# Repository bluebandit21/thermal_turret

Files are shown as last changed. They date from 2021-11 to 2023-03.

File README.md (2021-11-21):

Thermal Turret Project

#### **Useful documentation:**
SEN-09570 Infrared Thermometer: 
[Datasheet](https://www.sparkfun.com/datasheets/Sensors/Temperature/SEN-09570-datasheet-3901090614M005.pdf)

mediapipe 0.8.3.1 download link: https://pypi.org/project/mediapipe/0.8.3.1/#files

pip install some-package.whl

https://github.com/jiuqiant/mediapipe_python_aarch64

https://forums.developer.nvidia.com/t/google-mediapipe-real-time-hand-tracking-on-nano/80281/6

https://github.com/yockgen/mediapipe_jetson_nano

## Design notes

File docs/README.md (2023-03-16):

# Thermal Turret

This is a project developed as a proof of concept to a thermometer that can recognize human faces and direct a thermal laser at the forehead to measure the temperature of the person. This was initially built during the 2019 Covid19 Pandemic but has since been replaced by better systems and designs into 2020 and 2021.

All links to important documentation are located in [development-references](/docs/development-references.md)

## Basic Hardware Diagram

A more  thorough wiring sheet with descriptions and pins can be found in the [wiring](/docs/wiring.md) page

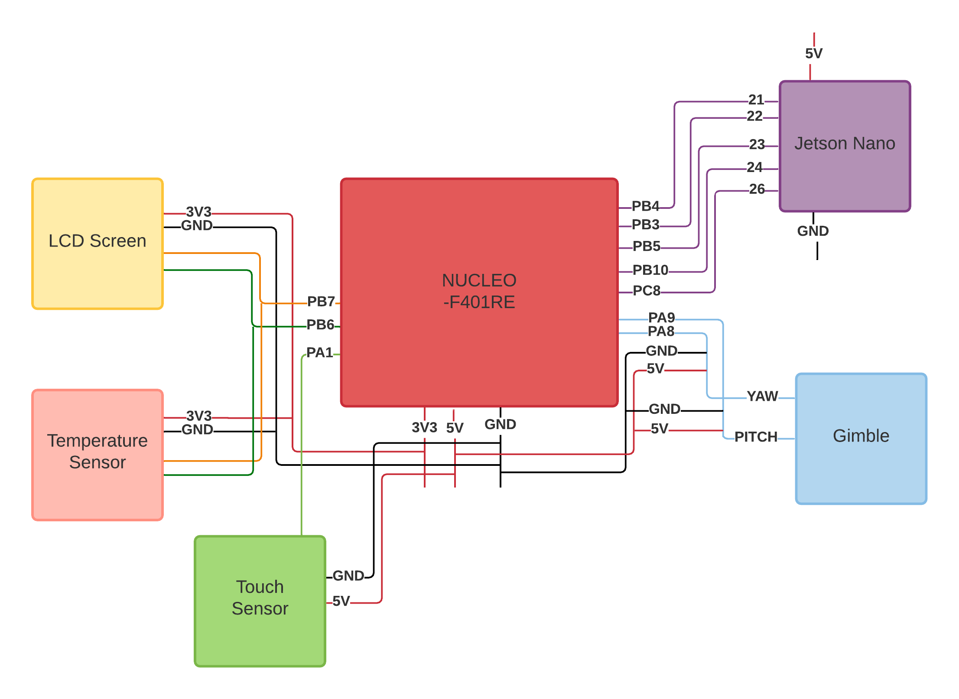
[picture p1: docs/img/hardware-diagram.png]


## Components and Codebase

### Infrared Thermometer
The thermal turret uses off the shelf consumer parts including a SEN-09570 infrared thermometer from sparkfun in a 3d printed case which can be foung in the [/cad](/cad) folder. The basic functionality can be seen by using the arduino project in the [/misc](/misc) folder. It also gives all information for locations of memory and important communication addresses for the temperature sensor.

There is also a TMP36 touch sensor for more fine tuned temperature readings in this specific prototype. When building the final prototype this is expected to be removed. It is added at this moment to compare between the SEN-09570 and itself for accuracy testing of the SEN-09570.

### Microcontroller
The microcontroller on this device is an STM32F401RETX nucleo development board. You can use the standard CubeMX IDE to compile and build the project on the nucleo seamlessly. You can follow the [wiring diagram](/docs/wiring.md) to see how to link all parts of the project. 

### Computer Vision

The computer vision device is a Jetson Nano. The developer kit which aided in cooling and running the jetson at high speeds. One can replace this with a suitable heat sink and fan combination. It uses OpenCV and a precompiled neural network for recognizing faces. There is a crontab to run the openCV script on startup as to not need setup beforehand. There is also a display linked to the Jetson Nano to display the view to the user. The Jetson Nano links with the Nucleo board by a parallel bus.

### Serial LCD

There is a serial LCD with RGB backlight linked with the project to display the temperature and other information. The reason for the RGB backlight is so that a user can see at a glance wether they are allowed to pass. The LCD will go green for safe temperatures, yellow if it wants to test you with the touch sensor and red if your temperature is obviously too high. 

## Basic Code Flow

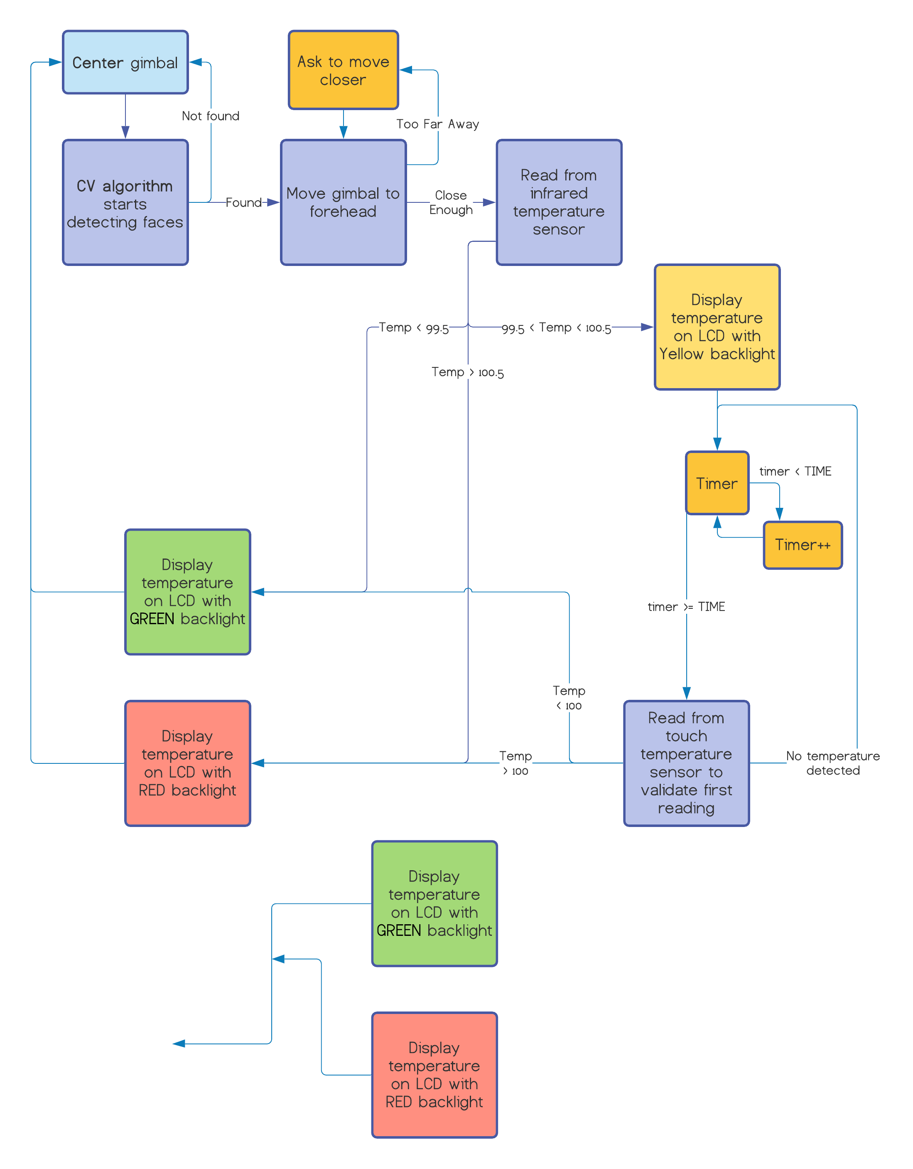
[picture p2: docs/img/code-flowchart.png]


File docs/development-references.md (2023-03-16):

#### **Useful documentation:**
SEN-09570 Infrared Thermometer: 
[Datasheet](https://www.sparkfun.com/datasheets/Sensors/Temperature/SEN-09570-datasheet-3901090614M005.pdf)

#### **Misc CV stuff:**

mediapipe 0.8.3.1 download link: https://pypi.org/project/mediapipe/0.8.3.1/#files

pip install some-package.whl

https://github.com/jiuqiant/mediapipe_python_aarch64

https://forums.developer.nvidia.com/t/google-mediapipe-real-time-hand-tracking-on-nano/80281/6

https://github.com/yockgen/mediapipe_jetson_nano

#### HEL_BUSY Fix
https://stackoverflow.com/questions/330793/how-to-initialize-a-struct-in-accordance-with-c-programming-language-standards

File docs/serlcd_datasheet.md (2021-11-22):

# LCD Codes for SparkFun RGB 3.3v Serial Open LCD display 
### with an attached Qwiic adapter

Rearranged for viewing by: Andrew Kent

Original information copied from SerLCD:
By: Gaston R. Williams

Original information copied from OpenLCD:
The OpenLCD display information is based based on code by
Nathan Seidle

## Addresses

Please Note: 0x72 is the 7-bit I2C address. If you are using a different language than Arduino you will probably
need to add the Read/Write bit to the end of the address. This means the default read address for the OpenLCD
is 0b.1110.0101 or 0xE5 and the write address is 0b.1110.0100 or 0xE4.

For more information see https://learn.sparkfun.com/tutorials/i2c
Note: This information expects the display to be listening at the default I2C address. If your display is not at 0x72, you can
do a hardware reset. Tie the RX pin to ground and power up OpenLCD. You should see the splash screen
then "System reset Power cycle me" and the backlight will begin to blink. Now power down OpenLCD and remove
the RX/GND jumper. OpenLCD is now reset.

To get this code to work, attach a Qwiic adapter to an OpenLCD. Use the Qwiic cable to attach adapter to a SparkFun Blackboard or
an Arduino Uno with the Qwiic shield.

 The OpenLCD has 4.7k pull up resistors on SDA and SCL. If you have other devices on the
 I2C bus then you may want to disable the pull up resistors by clearing the PU (pull up) jumper.

OpenLCD will work at 400kHz Fast I2C. Use the .setClock() call shown below to set the data rate
faster if needed.

## Command cheat sheet:

|  ASCII | DEC | HEX |
| :----: | :--- | :--- |
|  \| |  124 | 0x7C - Put into setting mode |
| Ctrl+c | 3 | 0x03 - Change width to 20 |
| Ctrl+d | 4 | 0x04 - Change width to 16 |
| Ctrl+e | 5 | 0x05 - Change lines to 4 |
| Ctrl+f | 6 | 0x06 - Change lines to 2 |
| Ctrl+g | 7 | 0x07 - Change lines to 1 |
| Ctrl+h | 8 | 0x08 - Software reset of the system |
| Ctrl+i | 9 | 0x09 - Enable/disable splash screen |
| Ctrl+j | 10 | 0x0A - Save currently displayed text as splash |
| Ctrl+k | 11 | 0x0B - Change baud to 2400bps |
| Ctrl+l | 12 | 0x0C - Change baud to 4800bps |
| Ctrl+m | 13 | 0x0D - Change baud to 9600bps |
| Ctrl+n | 14 | 0x0E - Change baud to 14400bps |
| Ctrl+o | 15 | 0x0F - Change baud to 19200bps |
| Ctrl+p | 16 | 0x10 - Change baud to 38400bps |
| Ctrl+q | 17 | 0x11 - Change baud to 57600bps |
| Ctrl+r | 18 | 0x12 - Change baud to 115200bps |
| Ctrl+s | 19 | 0x13 - Change baud to 230400bps |
| Ctrl+t | 20 | 0x14 - Change baud to 460800bps |
| Ctrl+u | 21 | 0x15 - Change baud to 921600bps |
| Ctrl+v | 22 | 0x16 - Change baud to 1000000bps |
| Ctrl+w | 23 | 0x17 - Change baud to 1200bps |
| Ctrl+x | 24 | 0x18 - Change the contrast. Follow Ctrl+x with number 0 to 255. 120 is default. |
| Ctrl+y | 25 | 0x19 - Change the TWI address. Follow Ctrl+x with number 0 to 255. 114 (0x72) is default. |
| Ctrl+z | 26 | 0x1A - Enable/disable ignore RX pin on startup (ignore emergency reset) |
|  + | 43 | 0x2B - Set RGB backlight with three following bytes, 0-255 |
|  , | 44 | 0x2C - Display current firmware version |
|  - | 45 | 0x2D - Clear display. Move cursor to home position. |
|  . | 46 | 0x2E - Enable system messages (ie, display 'Contrast: 5' when changed) |
|  / | 47 | 0x2F - Disable system messages (ie, don't display 'Contrast: 5' when changed) |
|  0 | 48 | 0x30 - Enable splash screen |
|  1 | 49 | 0x31 - Disable splash screen |
| | 128-157 | 0x80-0x9D - Set the primary backlight brightness. 128 = Off, 157 = 100%. |
| | 158-187 | 0x9E-0xBB - Set the green backlight brightness. 158 = Off, 187 = 100%. |
| | 188-217 | 0xBC-0xD9 - Set the blue backlight brightness. 188 = Off, 217 = 100%. |

For example, to change the baud rate to 115200 send 124 followed by 18.

## All Commands

```cpp
#define DISPLAY_ADDRESS1 0x72 //This is the default address of the OpenLCD
#define MAX_ROWS 4
#define MAX_COLUMNS 20

//OpenLCD command characters
#define SPECIAL_COMMAND 254  //Magic number for sending a special command
#define SETTING_COMMAND 0x7C //124, |, the pipe character: The command to change settings: baud, lines, width, backlight, splash, etc

//OpenLCD commands
#define CLEAR_COMMAND 0x2D					//45, -, the dash character: command to clear and home the display
#define CONTRAST_COMMAND 0x18				//Command to change the contrast setting
#define ADDRESS_COMMAND 0x19				//Command to change the i2c address
#define SET_RGB_COMMAND 0x2B				//43, +, the plus character: command to set backlight RGB value
#define ENABLE_SYSTEM_MESSAGE_DISPLAY 0x2E  //46, ., command to enable system messages being displayed
#define DISABLE_SYSTEM_MESSAGE_DISPLAY 0x2F //47, /, command to disable system messages being displayed
#define ENABLE_SPLASH_DISPLAY 0x30			//48, 0, command to enable splash screen at power on
#define DISABLE_SPLASH_DISPLAY 0x31			//49, 1, command to disable splash screen at power on
#define SAVE_CURRENT_DISPLAY_AS_SPLASH 0x0A //10, Ctrl+j, command to save current text on display as splash

// special commands
#define LCD_RETURNHOME 0x02
#define LCD_ENTRYMODESET 0x04
#define LCD_DISPLAYCONTROL 0x08
#define LCD_CURSORSHIFT 0x10
#define LCD_SETDDRAMADDR 0x80

// flags for display entry mode
#define LCD_ENTRYRIGHT 0x00
#define LCD_ENTRYLEFT 0x02
#define LCD_ENTRYSHIFTINCREMENT 0x01
#define LCD_ENTRYSHIFTDECREMENT 0x00

// flags for display on/off control
#define LCD_DISPLAYON 0x04
#define LCD_DISPLAYOFF 0x00
#define LCD_CURSORON 0x02
#define LCD_CURSOROFF 0x00
#define LCD_BLINKON 0x01
#define LCD_BLINKOFF 0x00

// flags for display/cursor shift
#define LCD_DISPLAYMOVE 0x08
#define LCD_CURSORMOVE 0x00
#define LCD_MOVERIGHT 0x04
#define LCD_MOVELEFT 0x00

```

## Writing to the Display

```cpp
/*
 * Write a byte to the display.
 * Required for Print.
 */
size_t SerLCD::write(uint8_t b)
{
  beginTransmission(); // transmit to device
  transmit(b);
  endTransmission(); //Stop transmission
  delay(10);         // wait a bit
  return 1;
} // write

/*
 * Write a character buffer to the display.
 * Required for Print.
 */
size_t SerLCD::write(const uint8_t *buffer, size_t size)
{
  size_t n = 0;
  beginTransmission(); // transmit to device
  while (size--)
  {
    transmit(*buffer++);
    n++;
  }                  //while
  endTransmission(); //Stop transmission
  delay(10);         //
  return n;
} //write

/*
 * Write a string to the display.
 * Required for Print.
 */
size_t SerLCD::write(const char *str)
{
  if (str == NULL)
    return 0;
  return write((const uint8_t *)str, strlen(str));
}
```

## Example Functions

```cpp
#define SETTING_COMMAND    0x7C //124, |, the pipe character: The command to change settings: baud, lines, width, backlight, splash, etc
#define SET_RGB_COMMAND    0x2B				//43, +, the plus character: command to set backlight RGB value
#define SPECIAL_COMMAND    254  //Magic number for sending a special command
#define LCD_DISPLAYCONTROL 0x08
#define LCD_ENTRYMODESET   0x04
#define CLEAR_COMMAND      0x2D					//45, -, the dash character: command to clear and home the display

/*
 * Initialize the display
 *
 */
void SerLCD::init()
{
  beginTransmission();
  transmit(SPECIAL_COMMAND);                      //Send special command character
  transmit(LCD_DISPLAYCONTROL | _displayControl); //Send the display command
  transmit(SPECIAL_COMMAND);                      //Send special command character
  transmit(LCD_ENTRYMODESET | _displayMode);      //Send the entry mode command
  transmit(SETTING_COMMAND);                      //Put LCD into setting mode
  transmit(CLEAR_COMMAND);                        //Send clear display command
  endTransmission();                              //Stop transmission
  delay(50);                                      //let things settle a bit
} //init

// New backlight function
void SerLCD::setFastBacklight(unsigned long rgb)
{
  // convert from hex triplet to byte values
  byte r = (rgb >> 16) & 0x0000FF;
  byte g = (rgb >> 8) & 0x0000FF;
  byte b = rgb & 0x0000FF;

  //send commands to the display to set backlights
  beginTransmission();       // transmit to device
  transmit(SETTING_COMMAND); //Send special command character
  transmit(SET_RGB_COMMAND); //Send the set RGB character '+' or plus
  transmit(r);               //Send the red value
  transmit(g);               //Send the green value
  transmit(b);               //Send the blue value
  endTransmission();         //Stop transmission
  delay(10);
} // setFastBacklight

/*
 *  Move the cursor multiple characters to the left.
 *
 *  count byte - number of characters to move
 */
void SerLCD::moveCursorLeft(byte count)
{

  beginTransmission(); // transmit to device

  for (int i = 0; i < count; i++)
  {
    transmit(SPECIAL_COMMAND); //Send special command character
    transmit(0x10);         //Send command code
  }                            // for
  endTransmission();           //Stop transmission

  delay(50); //Wait a bit longer for special display commands
} // moveCursorLeft

/*
 *  Move the cursor one character to the right.
 */
void SerLCD::moveCursorRight()
{
  beginTransmission(); // transmit to device

  for (int i = 0; i < count; i++)
  {
    transmit(SPECIAL_COMMAND); //Send special command character
    transmit(0x14);         //Send command code
  }                            // for
  endTransmission();           //Stop transmission

  delay(50); //Wait a bit longer for special display commands

/*
 * Send the clear command to the display.  This clears the
 * display and forces the cursor to return to the beginning
 * of the display.
 */
void SerLCD::clear()
{
  beginTransmission();       // transmit to device
  transmit(SETTING_COMMAND); //Put LCD into setting mode
  transmit(CLEAR_COMMAND);         //Send the command code
  endTransmission();         //Stop transmission

  delay(10); //Hang out for a bit
  delay(10); // a little extra delay after clear
}

```

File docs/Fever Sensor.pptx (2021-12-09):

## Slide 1

FEVER SENSOR
Abdulqader Khidir, Andrew Kent, Andrew Plotner, Anjana Malayarasan, Rutvi Shah

Hardware

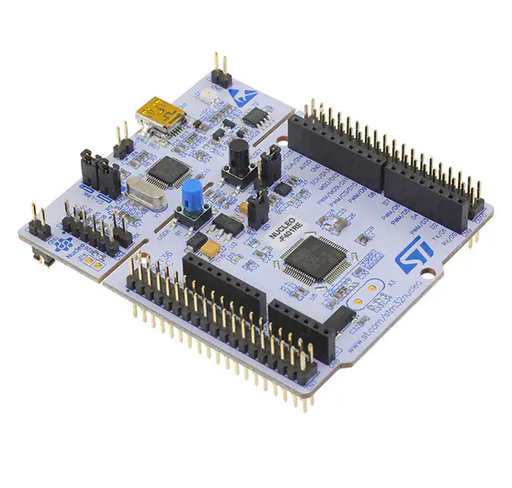
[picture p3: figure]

NUCLEO F401RE
STM32 microprocessor development board that controls the entire system. Takes input from camera/ Jetson Nano, and temperature sensors. Controls gimbal servos and sends output to displays.

Authors
Be proud of your work! Add the names of the people involved in this study. Don't forget to include titles and honorifics. We're proud of those too.

Affiliations
We're also proud of the institutions that we are with and support our research. Let's let them know by adding their names and logos here.

Research is often built on something that is already out there. Cite key references that you looked at while conducting your study.

Related literature

NVIDIA JETSON NANO
Small, powerful computer that controls the computer vision portion of the system. Detects the forehead and signals sensor.

Abstract

During the pandemic, taking human temperature readings from a distance is necessary in most establishments. Hiring to complete this task is costly and detrimental to workflow in job shortages. A device is being designed to test and verify users as they enter buildings or pass checkpoints. The device consists of a thermal sensor (Melexis MLX90614) and camera (Logitech C310) detecting human faces and following their movements using a 2 axis gimbal. When centered on a forehead, the thermal sensor reads and displays temperature data using a color LCD (Sparkfun LCD-16396). If the temperature is not satisfactory the system requires a user to hold a touch temperature sensor (Analog Devices TMP36) to get a more accurate reading of temperature. This approach improves accuracy and uniformity of temperature sensing and allows easy notice to interested parties of possibly hazardous associates.

Objective

Living in a time of a pandemic it is necessary to develop machines to improve the lives of others and keep the public safe. To reduce the staffing shortage in an impactful manner while keeping risk of exposure to a minimum.

Future Research

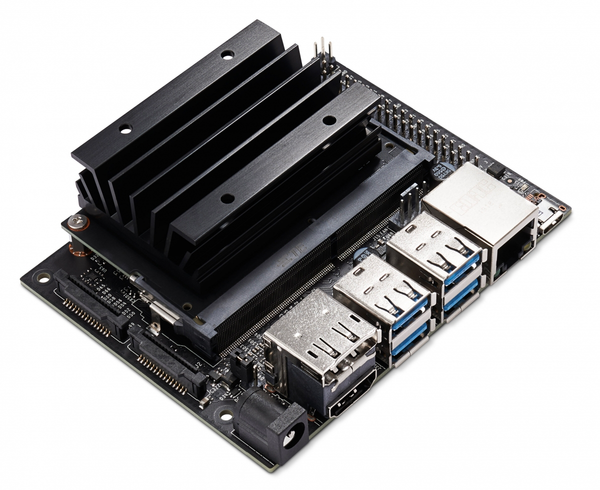
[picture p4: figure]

INFRARED TEMPERATURE SENSOR
No-contact Forehead Thermometer. Detects temperature and send output to microprocessor.

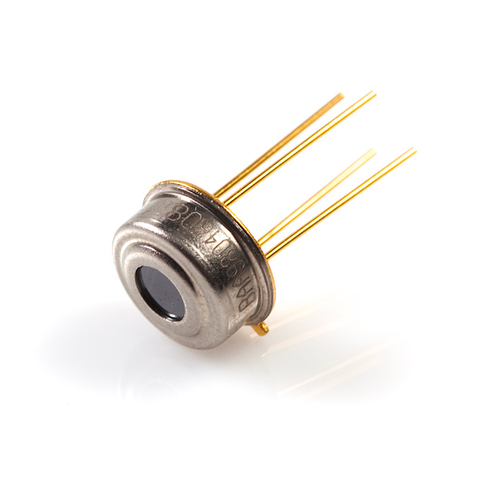
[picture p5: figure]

The need of long-range thermal sensors is of utmost importance, as it will allow medium to large scale testing of the system. A printed circuit board (PCB) for final connections is in development. Advancements in mounting hardware and case designs are necessary and are to reach further development after PCB design.

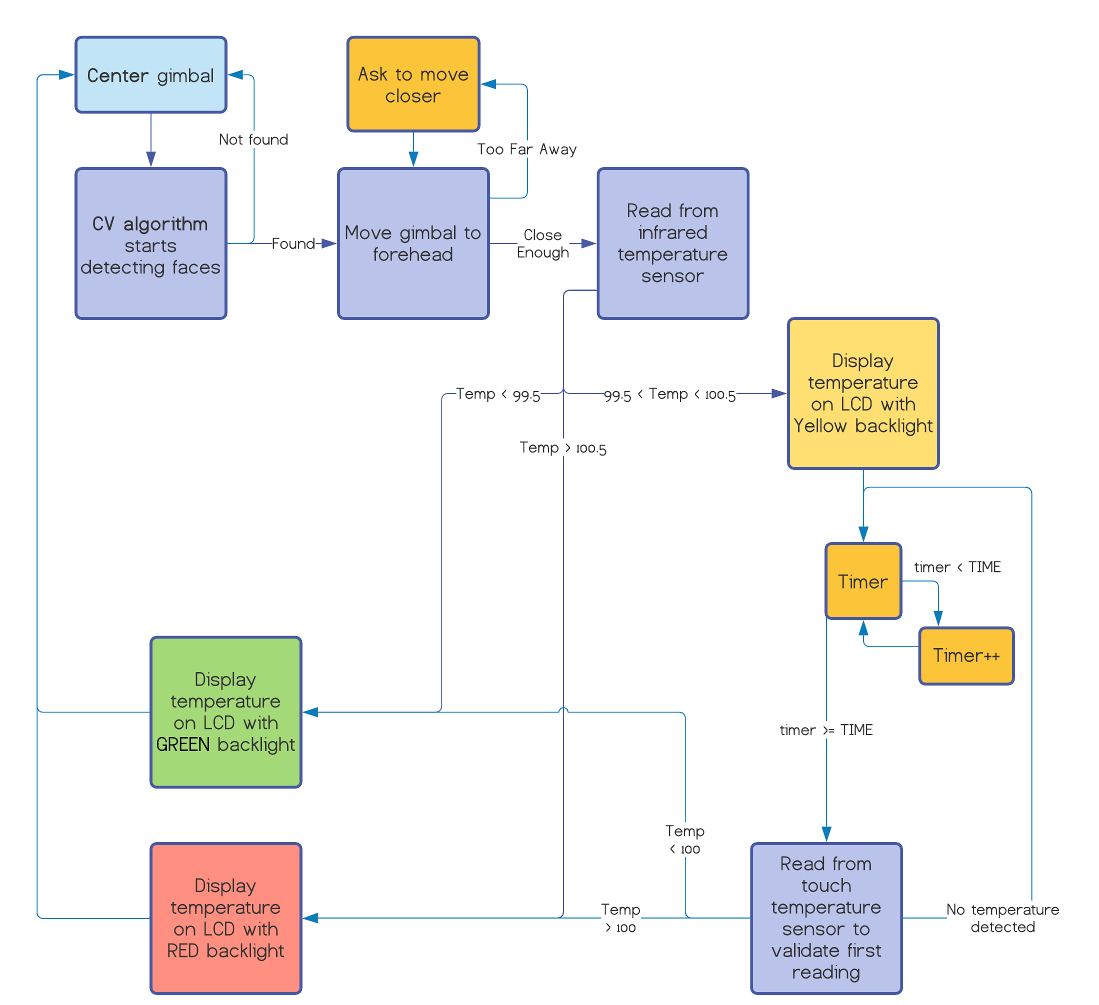
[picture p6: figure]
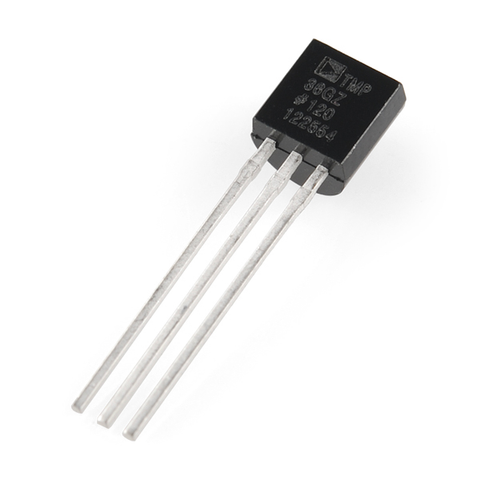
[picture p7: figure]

ANALOG CONTACT TEMPERATURE SENSOR
Touch temperature sensor provides voltage output proportional to the absolute temperature

SERVO GIMBAL
2-axis gimbal. Allows the camera to follow the movement of the person.

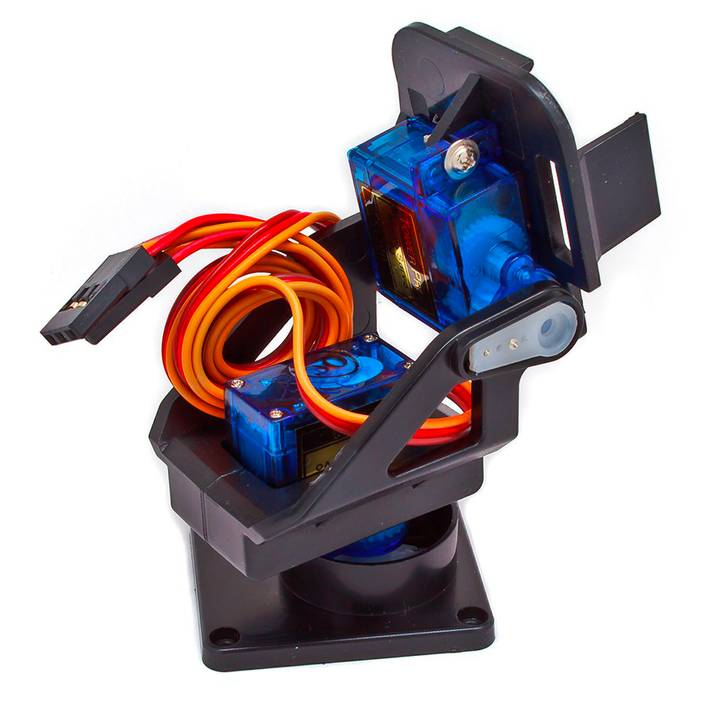
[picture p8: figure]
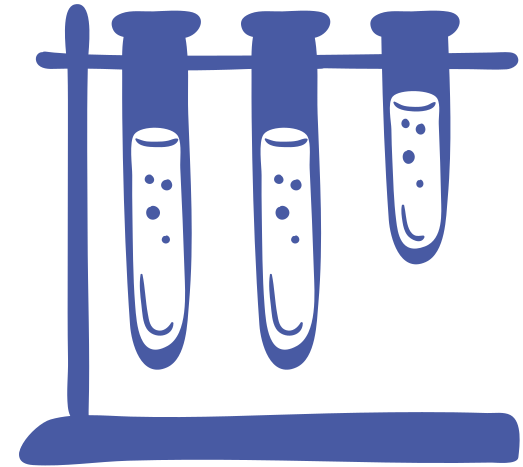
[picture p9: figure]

Code Logic

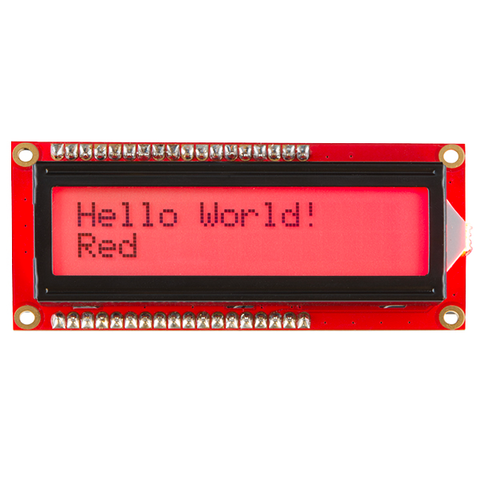
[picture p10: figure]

RGB LCD DISPLAY
Displays temperature and information in an easily visible format, also has a multicolor backlight to convey information at a glance.

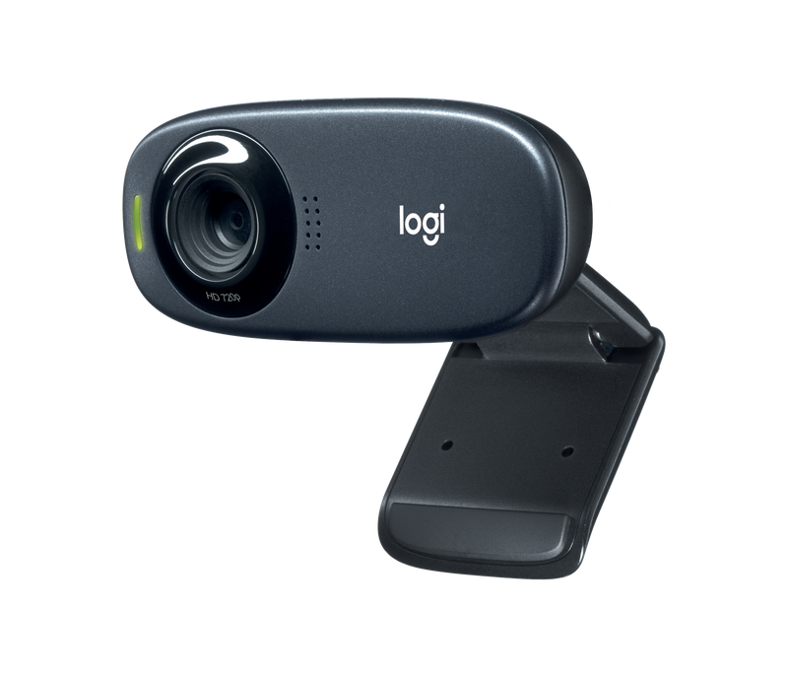
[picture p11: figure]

CAMERA
Allows the Jetson Nano to see the world around it and process human faces.

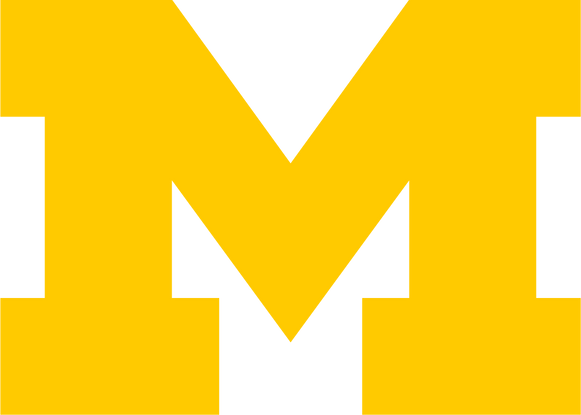
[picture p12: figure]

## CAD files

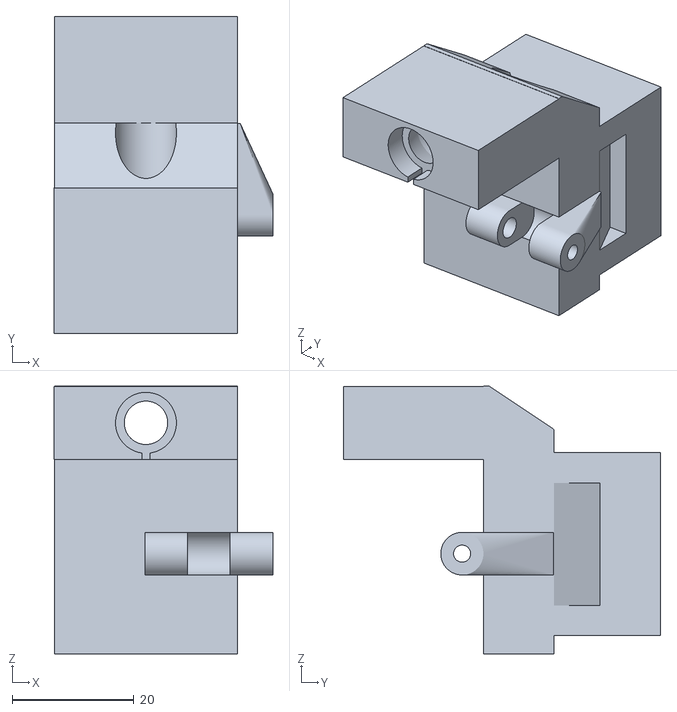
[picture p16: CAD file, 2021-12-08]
cad/stl/Full-test1 - v2.stl
35.9 x 52.1 x 44.0

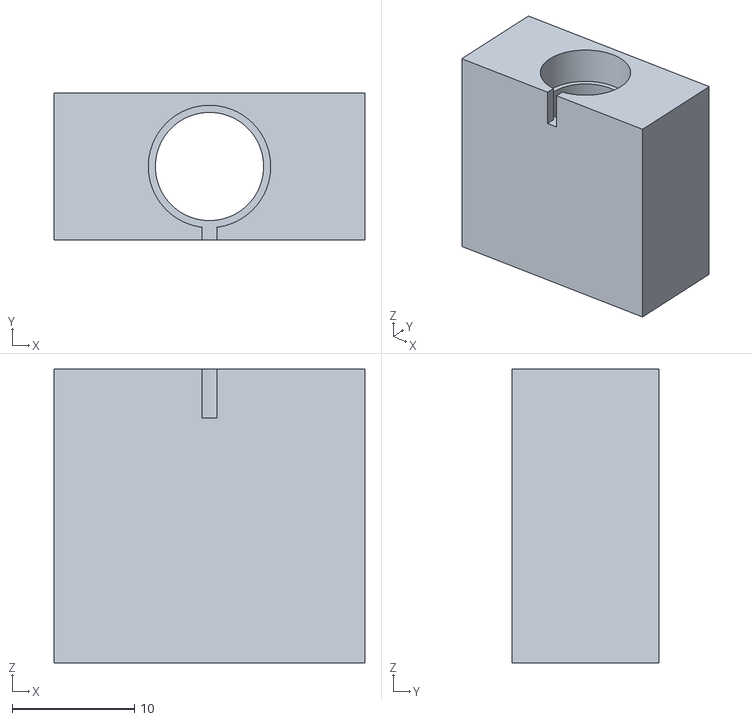
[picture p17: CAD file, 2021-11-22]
cad/stl/laser-test-2.stl
25.4 x 12.0 x 24.0

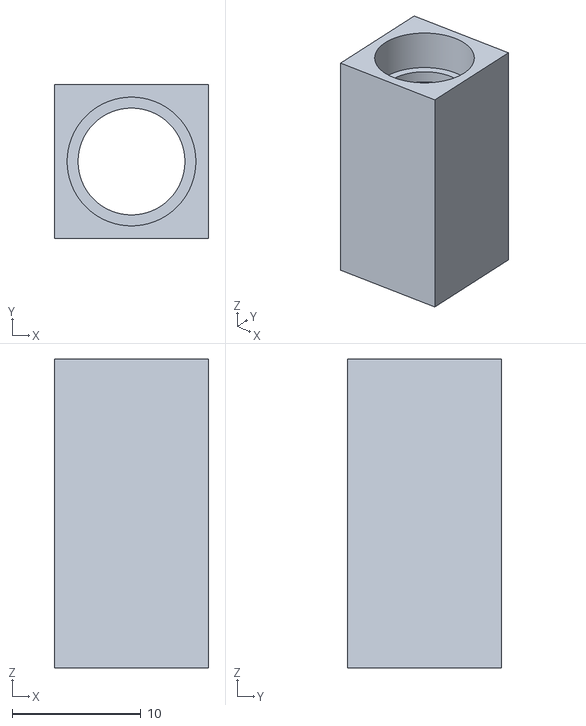
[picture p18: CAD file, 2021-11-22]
cad/stl/laser-test-1.stl
12.0 x 12.0 x 24.0

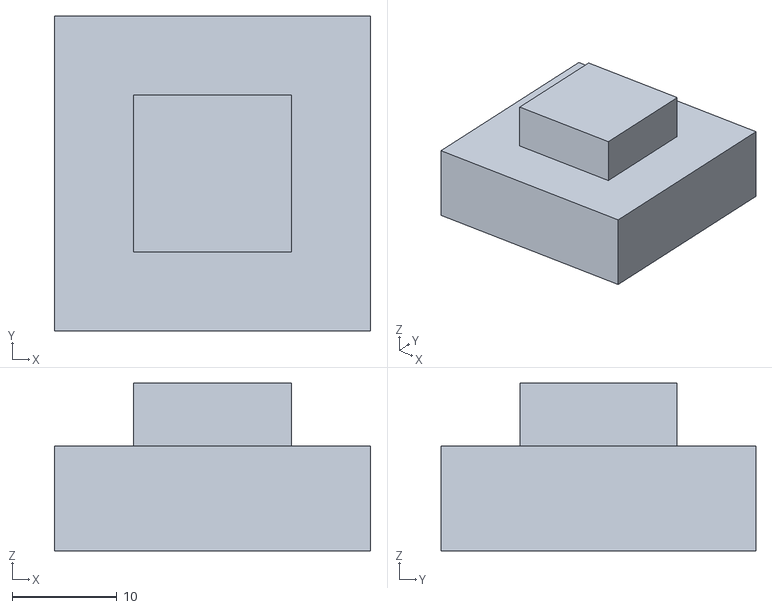
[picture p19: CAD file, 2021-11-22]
cad/stl/base-test-1.stl
30.2 x 30.1 x 16.1

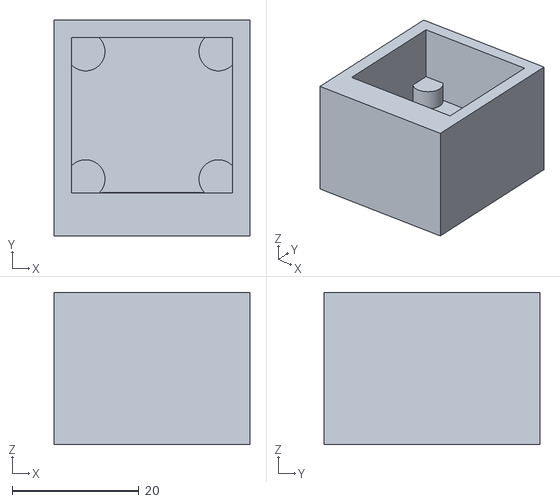
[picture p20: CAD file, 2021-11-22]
cad/stl/camera-test-2.stl
30.9 x 34.1 x 24.0

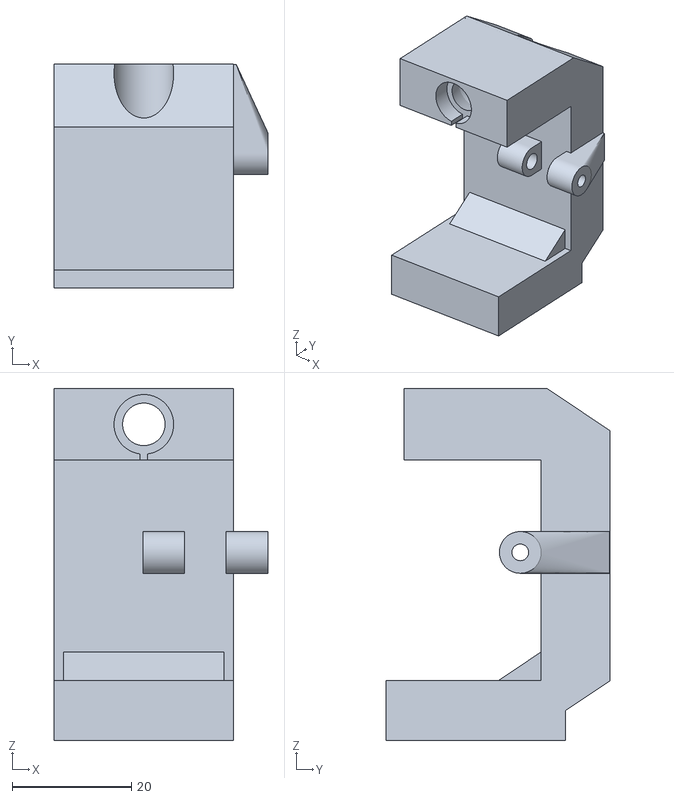
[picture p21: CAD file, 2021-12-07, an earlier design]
cad/stl/Full-test1.stl
35.9 x 37.6 x 59.0

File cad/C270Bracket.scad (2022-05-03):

$fn=90;
width=7;
height=7;

lampWidth=11;

smallScrew=2.8;
largeScrew=3.8;

mThreeHead=6;

lampScrew=5;

module lamp() {
	translate([40,0,0])
	difference() {
	cube([lampWidth, 40, lampWidth]);
	rotate([90,0,0])
		translate([lampWidth/2, lampWidth/2,-5])
		cylinder(r=smallScrew/2, h=10+1, center=true);

	rotate([0, 90, 0])
		translate([-lampWidth/2, 40-lampScrew, lampWidth/2])
		cylinder(r=lampScrew/2, h=lampWidth*2, center=true);
    }
}

module bracket() {
	difference() {

	translate([0, -width/2, 0])  // Goofed up my math in there somewhere
	hull() {
		rotate([0,90,0])
		translate([-width/2,width,0])
		cylinder(r=width/2 -1, h=width*3);
		translate([width*2/3, width*3, 0])
		cube([lampWidth, 1, width]);
	}

	translate([width, -1, -1])
		cube([width, width+1, width+3]);

	rotate([0,90,0])
		translate([-width/2, width/2, 0])
		cylinder(r=largeScrew/2, h=width);

		rotate([0,90,0])
		translate([-width/2, width/2, width*2])
		cylinder(r=smallScrew/2, h=width);

		rotate([90,0,0])
		translate([width*3/2, width/2, -width*3])
		cylinder(r=largeScrew/2, h=width*3);


		rotate([90,0,0])
			translate([width*3/2, width/2, -width-2])
			cylinder(r=mThreeHead/2, h=width);
	}
}

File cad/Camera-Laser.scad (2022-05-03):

/*
Created By Andrew Kent - SantaBunny
Built on - 11/16/2021

v1 - 11/16/2021
v2 - 12/07/2021



                       _.-''''''-._
                   _.-'            '-.
                 .'                _  '-
                /                -' '-_ '_
               /                 \     '8888
              /                   \    888888
             /                     \    8888
            /                       \
           /                         \
          /                           \
         /                             \
    ____/__  ______  ______  ______  ___\___
  /       \/      \/      \/      \/        \
 /                                           \
|                                            |
 \                                          /
  \                                        /
   \______/\______/\______/\______/\______/


Post-Fixes
------------------
D = diameter
I = Inner
L = Length
M = Milimeters
O = Outer
R = Radius
W = Width


*/
use <laser-module.scad>
use <camera-module.scad>
use <C270Bracket.scad>

////////////////////////////////////////////////////////////////////////////
// Everything in this secion is inches!!!! DO NOT USE BASE NUMBERS		  //
////////////////////////////////////////////////////////////////////////////
Laser_OD = 0.362; // inches
Laser_ID = 0.320; // inches
Laser_wireside_ID = 0.295; // inches
Laser_H = 0.160; // inches


Mount_Box_W = 1.185; //inches -- Max space 1.195
Mount_Box_L = 1.185; // inches -- hook top 1.06 -- Diff = 0.125
Mount_Box_H = 0.3937; // inches

// Rpi Cam
Camera_Board_W = 0.982; // inches
Camera_Board_L = 0.950; // inches <-- has 0.630 ribbon coming out of bottom center
Camera_D = 0.550; // inches

// Logitech C310
Camera_H = 1 + (7 / 32);
Camera_Front2Back = 0.75;

////////////////////////////////////////////////////////////////////////////
// Everything above this secion is inches!!!! DO NOT USE BASE NUMBERS	  //
////////////////////////////////////////////////////////////////////////////
spacer = 0.4;
Radius_Fragments = 200;
MM_scalar = 25.4;

Mount_Box_LM = Mount_Box_L * MM_scalar;
Mount_Box_WM = Mount_Box_W * MM_scalar;
Mount_Box_HM = Mount_Box_H * MM_scalar;
pyramid_Sidelength_M = sqrt(2 * pow(Mount_Box_LM, 2) );



// Rpi Cam
Camera_Board_LM = Camera_Board_L * MM_scalar;
Camera_Board_WM = Camera_Board_W * MM_scalar;


// Logitech C310
Camera_Front2Back_M = Camera_Front2Back * MM_scalar;
Camera_HM = Camera_H * MM_scalar;

// Laser
Laser_ODM = Laser_OD * MM_scalar;
Laser_wireside_IDM = Laser_wireside_ID * MM_scalar;
Laser_HM = Laser_H * MM_scalar;
box_size = Camera_Board_LM + 10; // 12 min // 25.4 - big enough for camera PBC
laser_box = 12;
box_thickness = 24; // 6
back_thickenss = box_thickness - Laser_HM - 4;

/////////////////////////////////////////////////////////////////////////////////////


// Mounting Base
translate([0,Mount_Box_LM * 3 / 2,Mount_Box_HM + 8])
cube($fn = Radius_Fragments, [Mount_Box_WM, Mount_Box_HM, Mount_Box_LM], 0);

// Base support cube
//translate([5,Mount_Box_LM * 5/4,Mount_Box_HM + 8])
//cube($fn = Radius_Fragments, [Mount_Box_WM - 10, Mount_Box_HM, Mount_Box_LM], 0);]\

// Pyramid support
translate([Mount_Box_LM/2,Mount_Box_LM * 5/4 + Mount_Box_LM/4,Mount_Box_HM + 8 + Mount_Box_LM/2])
rotate([90,-45,0])
cylinder($fn = 4, Mount_Box_LM/4, (pyramid_Sidelength_M - 10)/2, pyramid_Sidelength_M/2, 0);


// cube for cut bottom
translate([0,Mount_Box_LM * 5/4,Mount_Box_HM + Mount_Box_LM + 3 ])
cube($fn = Radius_Fragments, [Mount_Box_WM, Mount_Box_HM, 5], 0);
// cube for cut top
translate([0,Mount_Box_LM * 5/4,Mount_Box_HM + 8])
cube($fn = Radius_Fragments, [Mount_Box_WM, Mount_Box_HM, 5], 0);





//cube($fn = Radius_Fragments, [Mount_Box_WM - 10, Mount_Box_HM, Mount_Box_LM], 0);

//translate ([Mount_Box_WM / 4,Mount_Box_LM / 4,Mount_Box_HM])
//	cube($fn = Radius_Fragments, [Mount_Box_WM / 2, Mount_Box_LM, Mount_Box_HM - 4], 0);



// back support
	// Main up Block
difference() {
	union() {
	translate ([0,Mount_Box_LM * 5 / 4 - 11.57,Mount_Box_HM + 5])
		cube($fn = Radius_Fragments, [Mount_Box_WM,11.57,44],0);

	}

	// Hole for Laser wires
	translate([-((Camera_Board_LM + 10) - Mount_Box_WM) / 2,Mount_Box_LM / 2 + 12,Mount_Box_HM * 2 - 4 + Camera_HM])
	rotate([90,0,0]){
		translate([box_size / 2,laser_box / 2,box_thickness - 6.1]) {
			translate([0,0,-box_thickness -6])
			cylinder($fn = Radius_Fragments, back_thickenss + 12, Laser_ODM / 2 + spacer, Laser_ODM / 2 + spacer, 0);
		}
	}

	// Top angle aesthetic cut
	translate ([-0.1,Mount_Box_LM * 5 / 4 - 13.57,Mount_Box_HM * 2 + 10 + Camera_HM])
	rotate([-33.777,0,0])
		cube($fn = Radius_Fragments, [Mount_Box_WM + 2, 20, 20], 0);

	// cylinder cut for camera
	translate([bracket_centered_M  + camera_offset_M + 7,      Camera_Front2Back_M + 7,         Mount_Box_HM * 2 - 4+ (Camera_HM / 2)])
	rotate([0,90,0])
	cylinder($fn = Radius_Fragments, r=7/2, h=7);
}
/*
	// Back angle
translate([0,Mount_Box_LM,5])
	rotate([33.777,0,0])
		cube($fn = Radius_Fragments, [Mount_Box_WM,9,5], 0);

	//Back Support center angle
translate([1.5875,Mount_Box_LM - 10.0375,Mount_Box_HM - 4])
rotate([33.777,0,0])
	cube($fn = Radius_Fragments, [Mount_Box_LM - 3.175,12,4], 0);
*/


// Laser
translate([-((Camera_Board_LM + 6) - Mount_Box_WM) / 2,Mount_Box_LM / 2 + 12,Mount_Box_HM * 2 - 4 + Camera_HM])
rotate([90,0,0])
	Laser_Module(Camera_Board_LM + 6, 12, 24);

// Camera
// translate([Mount_Box_WM / 2 - (Camera_Board_WM + 6) + (Camera_Board_LM + 12) / 4,Mount_Box_LM / 2 + 12,Mount_Box_HM * 2])
// rotate ([90,0,0])
// Camera_Module();

bracket_centered_M = ((Mount_Box_LM) - 21) / 2;
camera_offset_M = 13/32 * MM_scalar;

difference() {
	translate([bracket_centered_M  + camera_offset_M,   Camera_Front2Back_M,   Mount_Box_HM * 2 - 4+ (Camera_HM / 2)  - 7/2])
	bracket();

	// cylinder cut for camera
	translate([bracket_centered_M  + camera_offset_M + 7,      Camera_Front2Back_M + 7,         Mount_Box_HM * 2 - 4+ (Camera_HM / 2)])
	rotate([0,90,0])
	cylinder($fn = Radius_Fragments, r=7/2, h=7);
}

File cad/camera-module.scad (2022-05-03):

/*
Created By Andrew Kent - SantaBunny
Built on - 11/21/2021

v1 - 11/21/2021



					  _.-''''''-._
				  _.-'			  '-.
				.'				  _  '-
			   /				-' '-_ '_
			  /			        \     '8888
			 /					 \    888888
			/					  \    8888
		   /					   \
		  /						    \
		 /						     \
		/						      \
   ____/__  ______  ______  ______  ___\___
  /       \/      \/      \/      \/       \
 /										    \
|										     |
 \										    /
  \										   /
   \______/\______/\______/\______/\______/


Post-Fixes
------------------
D = diameter
I = Inner
L = Length
M = Milimeters
O = Outer
R = Radius
W = Width


*/

Camera_Board_W = 0.950; // inches -- top to bottom
Camera_Board_L = 0.982; // inches <-- has 0.630 ribbon coming out of bottom center -- left to right

Camera_D = 0.550; // inches


//////////////////////////////////////////////
Radius_Fragments = 200;
MM_scalar = 25.4;

spacer = 0.4;
box_thickness = 24;

Camera_Board_LM = Camera_Board_L * MM_scalar;
Camera_Board_WM = Camera_Board_W * MM_scalar;
Camera_DM = Camera_D * MM_scalar;
Ribbon_M = 16.002;


screw_center_M = 0.325 * MM_scalar;
support_RM = 0.12 * MM_scalar;
support_depth_M = 5;

/////////////////////////////////////////////

Camera_Module();

module Camera_Module() {
//main body
	union() {
		difference() {
			translate([0,-4,0])
				cube($fn = Radius_Fragments, [Camera_Board_LM+6, Camera_Board_WM+10, box_thickness],0);
			// Camera Board
			translate([2.8,2.8,box_thickness-Camera_DM -1])
				cube($fn = Radius_Fragments, [Camera_Board_LM+spacer, Camera_Board_WM+spacer, box_thickness - Camera_DM +support_depth_M], 0);
			// Ribbon Cable
			translate([(Camera_Board_LM+6 - Ribbon_M) / 2,-3.1,-0.1])
				cube($fn = Radius_Fragments, [Ribbon_M+spacer, 6, box_thickness - Camera_DM + 6], 0);
		};
		translate([5,Camera_Board_WM + 1,box_thickness - Camera_DM - 2])
		rotate([0,0,90])
			Corner();
		translate([Camera_Board_LM + 1,Camera_Board_WM + 1,box_thickness - Camera_DM - 2])
		rotate([0,0,0])
			Corner();
		translate([5,5,box_thickness - Camera_DM - 2])
		rotate([0,0,180])
			Corner();
		translate([Camera_Board_LM + 1,5,box_thickness - Camera_DM - 2])
		rotate([0,0,-90])
			Corner();
		//cylinder($fn = Radius_Fragments, support_depth_M, support_RM, support_RM, 0);
	};
};

module Corner() {
	union() {
		translate([0,0,0])
			cube($fn = Radius_Fragments, [support_RM,support_RM,support_depth_M], 0);
		cylinder($fn = Radius_Fragments, support_depth_M, support_RM, support_RM, 0);
	}
}

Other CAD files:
cad/stl/camera-test-1.stl
cad/case.scad
cad/laser-module.scad
cad/lcdcase.scad

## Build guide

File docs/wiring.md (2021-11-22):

### **Gimbal:**  
Servomotors red wires need to be connected to +5 V, brown wires need to be connected to ground.  
The orange wire of the pitch servo needs to be connected to pin A9 (labelled "D8" on board surface)  
The orange wire of the yaw servo needs to be connected to pin A8 (labelled "D7" on board surface)  

### **Infrared thermometer:**  
Red wire needs to be connected to +3.3 V (not 5V!!!!!!!!!!!!!), black to ground, with a 0.1 uF decoupling capacitor between the two  
Green (SCL) needs to be connected to pin B6 (ninth pin down on the middle row of pins on the right (oriented with ST logo on bottom))  
Orange (SDA) needs to be connected to pin B7 (ninth pin from the bottom on the left row of pins on the left (oriented with ST logo on bottom))  

### **Contact thermometer:**  
With flat side of device oriented up and bottom of device (pin side) pointed towards sky,  
Left leg connected to voltage supply (3.3v or 5v both fine, operating range is 2.7 - 5.5 volts)
Right leg connected to ground
0.1 uF capacitor (labelled "BC 104") between high and low pins

Output pin of op-amp circuit connected to pin A1 (fifth pin from the bottom on the middle row of pins on the left (oriented with ST logo on bottom))

TODO: // describe op-amp circuit coming off of data pin

### **Vision interface:**
Target left wire connected to pin PB3  (Fourth pin from bottom on middle row of pins on the right (oriented with ST logo on bottom)), other end connected to Jetson Nano pin //TODO: ADD ME

Target right wire connected to pin PB4 (Sixth pin from bottom on middle row of pins on the right (oriented with ST logo on bottom)), other end connected to Jetson Nano pin //TODO: ADD ME

Target up wire connected to pin PB5    (Fifth pin from bottom on middle row of pins on the right (oriented with ST logo on bottom)), other end connected to Jetson Nano pin //TODO: ADD ME

Target down wire connected to pin PB10 (Seventh pin from bottom on middle row of pins on the right (oriented with ST logo on bottom)), other end connected to Jetson Nano pin //TODO: ADD ME

### **Logic Analyzer:**
Yellow wire connected to CH2 is SDA, grey wire connected to CH3 is SCL
(If these are set up properly, logic analyzer very nicely properly logs output for us)

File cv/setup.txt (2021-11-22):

https://github.com/codeniko/shape_predictor_81_face_landmarks
https://forums.developer.nvidia.com/t/install-scikit-image/122912/12

Crontab entry:
@reboot python3 /home/abdulqader/Documents/eecs373/thermal_turret/cv/Videos/web$

This starts our CV on boot headless

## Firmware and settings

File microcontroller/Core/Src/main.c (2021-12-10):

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
/* Includes ------------------------------------------------------------------*/
#include "main.h"

/* USER CODE BEGIN Includes */
#include "math.h"
#include "OpenLCD.h"
#include "MLX90614.h"
#include "stdio.h"
#include "float.h"


/* USER CODE END Includes */

/* USER CODE BEGIN PTD */

//------------------------MISC TYPES------------------------------------------
typedef struct I2C_Module
{
  I2C_HandleTypeDef   instance;
  uint16_t            sdaPin;
  GPIO_TypeDef*       sdaPort;
  uint16_t            sclPin;
  GPIO_TypeDef*       sclPort;
}I2C_Module;



enum SYSTEM_STATE{
	START, /* Nobody centered frame for a while / just powered on. Display
			* nothing on the display, camera heads to (0,0) or tracks towards forehead if present */
	CENTERED, /* We just saw a centered forehead in frame. Take the temperature. If it's not high enough,
	           * tell the user to move closer to the camera on the display */
	TOUCH_WAIT, /* Tell the user to touch the contact sensor and show yellow, along with temperature reading.
				 * Wait for them to touch the contact sensor (i.e. contact sensor goes above ambient)
				 * If they don't after some timeout, move back to RESET*/
	TOUCH_HOLD, /* Have them hodl for a while after detecting initial */
	PAUSE /* Delay for a brief period of time to let the user see the thing, then go to START*/
};



/* USER CODE END PTD */

/* USER CODE BEGIN PD */
#define LASER_SMBUS_ADDRESS 0xB4

#define LASER_TOBJ1_ADDRESS 0x007

#define COMMAND_READ 0x1

//------------------------GIMBAL CONSTANTS-------------------------------------
//Determined experimentally (the datasheet lies)
#define SERVO_PULSE_WIDTH_TICKS 35471
#define SERVO_YAW_NEUTRAL_TICKS  2700
//Range from neutral to +max or -max in ticks
#define SERVO_YAW_RANGE_TICKS 1700 //Determined experimentally
#define SERVO_YAW_MAX_ANGLE 95 //Determined experimentally

#define SERVO_PITCH_NEUTRAL_TICKS  2600 //TODO: Measure better? These still feel slightly off
//Range from neutral to +max or -max in ticks
#define SERVO_PITCH_RANGE_TICKS 1700 //TODO: Measure
#define SERVO_PITCH_MAX_ANGLE 95 //TODO: Measure
#define SERVO_PITCH_MAX_SAFE_ANGLE_MIN 40
#define SERVO_PITCH_MAX_SAFE_ANGLE_MAX -75

//------------------------TOUCH THERMOMETER CONSTANTS-----------------------------
const float R1 = 32.66;  //kOhms
const float R2 = 9.866; //kOhms

//---------------------------VISION INTERFACE CONSTANTS---------------------------

GPIO_TypeDef* VISION_LEFT_BANK = GPIOB;
GPIO_TypeDef* VISION_RIGHT_BANK = GPIOB;
GPIO_TypeDef* VISION_UP_BANK = GPIOB;
GPIO_TypeDef* VISION_DOWN_BANK = GPIOB;
GPIO_TypeDef* VISION_SEES_FACE_BANK = GPIOC;
uint16_t VISION_LEFT_PIN = GPIO_PIN_3;
uint16_t VISION_RIGHT_PIN = GPIO_PIN_4;
uint16_t VISION_UP_PIN = GPIO_PIN_5;
uint16_t VISION_DOWN_PIN = GPIO_PIN_10;
uint16_t VISION_SEES_FACE_PIN = GPIO_PIN_8;



//---------------------------STATE LOGIC CONSTANTS----------------------
#define TEMP_SAFE 78.00 //TODO: Adjust me
#define TEMP_UNSAFE 86.00 //TODO: Adjust me
#define TEMP_THRESHOLD 76.00 //TODO: Adjust me
#define RESET_TIMEOUT 20 //TODO: Adjust me
#define DELAY_TIMEOUT 40 //TODO: Adjust me
#define TOUCH_TEMP_THRESHOLD 73.0 //TODO: Adjust me
#define TOUCH_TIMEOUT 100 //TODO: Adjust me
#define TOUCH_TEMP_SAFE 73.5 //TODO: Adjust me
#define TOUCH_HOLD_COUNT 100 //TODO: Adjust me
#define MOVE_SPEED 1

const char* MESSAGE_SEARCHING = "Searching...";
const char* MESSAGE_MOVE_CLOSER = "Move closer";
const char* MESSAGE_TOUCH = "Touch sensor";
const char* MESSAGE_HOLD = "Continue hold";



/* USER CODE END PD */

ADC_HandleTypeDef hadc1;

I2C_HandleTypeDef hi2c1;

TIM_HandleTypeDef htim1;

UART_HandleTypeDef huart2;

void SystemClock_Config(void);
static void MX_GPIO_Init(void);
static void MX_I2C1_Init(void);
static void MX_TIM1_Init(void);
static void MX_ADC1_Init(void);
static void MX_USART2_UART_Init(void);
/* USER CODE BEGIN PFP */

#define I2C1_SCL_Pin GPIO_PIN_6
#define I2C1_SCL_GPIO_Port GPIOB
#define I2C1_SDA_Pin GPIO_PIN_7
#define I2C1_SDA_GPIO_Port GPIOB


/* USER CODE END PFP */

/* USER CODE BEGIN 0 */

//------------------------CONTACT THERMOMETER DRIVERS--------------------------

float read_temperature_blocking();

/* float read_temperature_blocking()
 *  Reports temperature read by contact temperature sensor and returns as a float degrees Fahrenheit
 *  This is a blocking function and will wait several cycles for the ADC to finish converting.
 */
float read_temperature_blocking(){
	  HAL_ADC_Start(&hadc1);//start conversion
	  HAL_ADC_PollForConversion(&hadc1, 0xFFFFFFFF);
	  float RAW_COUNT = HAL_ADC_GetValue(&hadc1);
	  float voltage = RAW_COUNT * 3.3 / 4096;
	  float corrected_voltage = (voltage * R2 / (R1+R2) ) - 0.5; //Remove DC offset, de scale
	  float temp_c = corrected_voltage * 100;
	  float temp_f = temp_c * 1.8  + 32;

	  return temp_f;
}

//------------------------GIMBAL DRIVERS---------------------------------------

void initialize_gimbal();
int set_gimbal_angles(int yaw, int pitch);


/* void initialize_gimbal()
 *  Initializes hardware timers for gimbals and sets init position to (0,0)
 */
void initialize_gimbal(){
	//Start hardware timers
	HAL_TIM_PWM_Start(&htim1, TIM_CHANNEL_1);
	HAL_TIM_IC_Start_IT(&htim1, TIM_CHANNEL_1);
	HAL_TIM_PWM_Start(&htim1, TIM_CHANNEL_2);
	HAL_TIM_IC_Start_IT(&htim1, TIM_CHANNEL_2);

	//Move to starting position
	set_gimbal_angles(0,0);
}

/* int target_gimbal_angles(short yaw, short pitch)
 *  Moves gimbal to specified position of yaw and pitch.
 *  Yaw can range from -95 degrees to 95 degrees
 *  Pitch can range from //TODO: Measure me
 *  If a move would cause physical damage to the gimbal, or make the servos unhappy,
 *   it is not made and -1 is returned as an error status.
 */
int set_gimbal_angles(int yaw, int pitch){
	pitch-=40; //Set neutral up
	if((yaw > SERVO_YAW_MAX_ANGLE) || (yaw < -SERVO_YAW_MAX_ANGLE)\
			|| (pitch > SERVO_PITCH_MAX_SAFE_ANGLE_MIN) || (pitch < SERVO_PITCH_MAX_SAFE_ANGLE_MAX)){
		//Refuse to do this move; it'd cause bad things to occur physically
		//TODO: Add logging here
		return -1;
	}
	int yaw_pulse_width = SERVO_YAW_NEUTRAL_TICKS + (yaw * SERVO_YAW_RANGE_TICKS) / SERVO_YAW_MAX_ANGLE;
	__HAL_TIM_SET_COMPARE(&htim1, TIM_CHANNEL_1, yaw_pulse_width);

	int pitch_pulse_width = SERVO_PITCH_NEUTRAL_TICKS + (pitch * SERVO_PITCH_RANGE_TICKS) / SERVO_PITCH_MAX_ANGLE;
	__HAL_TIM_SET_COMPARE(&htim1, TIM_CHANNEL_2, pitch_pulse_width);
	return 0;

}


//-----------------------VISION INTERFACE DRIVERS--------------------------------------

GPIO_PinState target_left();
GPIO_PinState target_right();
GPIO_PinState target_up();
GPIO_PinState target_down();
GPIO_PinState sees_face();

GPIO_PinState target_left(){
	return HAL_GPIO_ReadPin(VISION_LEFT_BANK, VISION_LEFT_PIN);
}
GPIO_PinState target_right(){
	return HAL_GPIO_ReadPin(VISION_RIGHT_BANK, VISION_RIGHT_PIN);
}
GPIO_PinState target_up(){
	return HAL_GPIO_ReadPin(VISION_UP_BANK, VISION_UP_PIN);
}
GPIO_PinState target_down(){
	return HAL_GPIO_ReadPin(VISION_DOWN_BANK, VISION_DOWN_PIN);
}

GPIO_PinState sees_face(){
	return HAL_GPIO_ReadPin(VISION_SEES_FACE_BANK, VISION_SEES_FACE_PIN);
}

//-------------------------MISC------------------------------------------------------
void clear_i2c_busy();
void I2C_ClearBusyFlagErratum(struct I2C_Module* i2c);


/* void I2C_ClearBusyFlagErratum(struct I2C_Module* i2c)
 * Does magic to reset the HAL_Busy I2C state when it gets stuck there sometimes.
 * Sourced from https://electronics.stackexchange.com/questions/267972/i2c-busy-flag-strange-behaviour
 */
void I2C_ClearBusyFlagErratum(struct I2C_Module* i2c)
{
  GPIO_InitTypeDef GPIO_InitStructure;

  // 1. Clear PE bit.
  i2c->instance.Instance->CR1 &= ~(0x0001);

  //  2. Configure the SCL and SDA I/Os as General Purpose Output Open-Drain, High level (Write 1 to GPIOx_ODR).
  GPIO_InitStructure.Mode         = GPIO_MODE_OUTPUT_OD;
  GPIO_InitStructure.Alternate    = GPIO_AF4_I2C1;
  GPIO_InitStructure.Pull         = GPIO_PULLUP;
  GPIO_InitStructure.Speed        = GPIO_SPEED_FREQ_HIGH;

  GPIO_InitStructure.Pin          = i2c->sclPin;
  HAL_GPIO_Init(i2c->sclPort, &GPIO_InitStructure);
  HAL_GPIO_WritePin(i2c->sclPort, i2c->sclPin, GPIO_PIN_SET);

  GPIO_InitStructure.Pin          = i2c->sdaPin;
  HAL_GPIO_Init(i2c->sdaPort, &GPIO_InitStructure);
  HAL_GPIO_WritePin(i2c->sdaPort, i2c->sdaPin, GPIO_PIN_SET);

  // 3. Check SCL and SDA High level in GPIOx_IDR.
  while (GPIO_PIN_SET != HAL_GPIO_ReadPin(i2c->sclPort, i2c->sclPin))
  {
    asm("nop");
  }

  while (GPIO_PIN_SET != HAL_GPIO_ReadPin(i2c->sdaPort, i2c->sdaPin))
  {
    asm("nop");
  }

  // 4. Configure the SDA I/O as General Purpose Output Open-Drain, Low level (Write 0 to GPIOx_ODR).
  HAL_GPIO_WritePin(i2c->sdaPort, i2c->sdaPin, GPIO_PIN_RESET);

  //  5. Check SDA Low level in GPIOx_IDR.
  while (GPIO_PIN_RESET != HAL_GPIO_ReadPin(i2c->sdaPort, i2c->sdaPin))
  {
    asm("nop");
  }

  // 6. Configure the SCL I/O as General Purpose Output Open-Drain, Low level (Write 0 to GPIOx_ODR).
  HAL_GPIO_WritePin(i2c->sclPort, i2c->sclPin, GPIO_PIN_RESET);

  //  7. Check SCL Low level in GPIOx_IDR.
  while (GPIO_PIN_RESET != HAL_GPIO_ReadPin(i2c->sclPort, i2c->sclPin))
  {
    asm("nop");
  }

  // 8. Configure the SCL I/O as General Purpose Output Open-Drain, High level (Write 1 to GPIOx_ODR).
  HAL_GPIO_WritePin(i2c->sclPort, i2c->sclPin, GPIO_PIN_SET);

  // 9. Check SCL High level in GPIOx_IDR.
  while (GPIO_PIN_SET != HAL_GPIO_ReadPin(i2c->sclPort, i2c->sclPin))
  {
    asm("nop");
  }

  // 10. Configure the SDA I/O as General Purpose Output Open-Drain , High level (Write 1 to GPIOx_ODR).
  HAL_GPIO_WritePin(i2c->sdaPort, i2c->sdaPin, GPIO_PIN_SET);

  // 11. Check SDA High level in GPIOx_IDR.
  while (GPIO_PIN_SET != HAL_GPIO_ReadPin(i2c->sdaPort, i2c->sdaPin))
  {
    asm("nop");
  }

  // 12. Configure the SCL and SDA I/Os as Alternate function Open-Drain.
  GPIO_InitStructure.Mode         = GPIO_MODE_AF_OD;
  GPIO_InitStructure.Alternate    = GPIO_AF4_I2C1;

  GPIO_InitStructure.Pin          = i2c->sclPin;
  HAL_GPIO_Init(i2c->sclPort, &GPIO_InitStructure);

  GPIO_InitStructure.Pin          = i2c->sdaPin;
  HAL_GPIO_Init(i2c->sdaPort, &GPIO_InitStructure);

  // 13. Set SWRST bit in I2Cx_CR1 register.
  i2c->instance.Instance->CR1 |= 0x8000;

  asm("nop");

  // 14. Clear SWRST bit in I2Cx_CR1 register.
  i2c->instance.Instance->CR1 &= ~0x8000;

  asm("nop");

  // 15. Enable the I2C peripheral by setting the PE bit in I2Cx_CR1 register
  i2c->instance.Instance->CR1 |= 0x0001;

  // Call initialization function.
  HAL_I2C_Init(&(i2c->instance));
}



/* void clear_i2c_busy()
 *  Sometimes the HAL I2C implementation randomly gets stuck in HAL_BUSY
 *  This fixes it. It is hacky and awful, but so is the HAL library apparently.
 */
void clear_i2c_busy(){
	//This is a horrible hack and shouldn't be neccesary. Yet, it is.
	I2C_Module I2C;
	I2C.instance = hi2c1;
	I2C.sclPin = I2C1_SCL_Pin;
	I2C.sclPort = I2C1_SCL_GPIO_Port;
	I2C.sdaPin = I2C1_SDA_Pin;
	I2C.sdaPort = I2C1_SDA_GPIO_Port;

	I2C_ClearBusyFlagErratum(&I2C);
}

void initialize_lcd(){
	 OpenLCD_begin(&hi2c1);
	 OpenLCD_setContrast(0);
	 OpenLCD_setFastBacklightrgb(128, 128, 128);
}



/* USER CODE END 0 */

/**
  * @brief  The application entry point.
  * @retval int
  */
int main(void)
{
  /* MCU Configuration--------------------------------------------------------*/

  /* Reset of all peripherals, Initializes the Flash interface and the Systick. */
  HAL_Init();

  /* USER CODE BEGIN Init */


  // 4 inputs from Jetson Nano
  //- Up
  //- Down
  //- Left
  //- Right
  //If none are high, laser is aimed properly.

  // 2 PWM Outputs

  // 2 I2C I/O
  // Temp Sens
  // Display

  // ADC for touch

  /* USER CODE END Init */

  /* Configure the system clock */
  SystemClock_Config();

  /* Initialize all configured peripherals */
  MX_GPIO_Init();
  MX_I2C1_Init();
  MX_TIM1_Init();
  MX_ADC1_Init();
  MX_USART2_UART_Init();
  /* USER CODE BEGIN 2 */


  initialize_gimbal();
  initialize_lcd();

  clear_i2c_busy();


  MLX_IRTherm();
  bool MLX_OK = MLX_begin(&hi2c1);
  if (!MLX_OK){
	  printf("ERROR: MLX90614: MLX_begin(): Not Connected");
  }
  MLX_setUnit(TEMP_F);


  /* USER CODE END 2 */

  /* Infinite loop */
  /* USER CODE BEGIN WHILE */
  int yaw = 0;
  int pitch = 0;
  long counter = 0;
  float locked_temp;

  enum SYSTEM_STATE state = START;

  while (1) {
    /* USER CODE END WHILE */

    /* USER CODE BEGIN 3 */
	  clear_i2c_busy();

	  //--------------------------GIMBAL TRACKING LOGIC: ALWAYS RUNS----------------------

	  if(sees_face()){
		  if(target_left()){
			  printf("Targeting left\r\n");
			  if(yaw < SERVO_YAW_MAX_ANGLE){
				yaw = yaw + MOVE_SPEED;
			  }
		  }
		  if(target_right()){
			  printf("Targeting right\r\n");
			  if(yaw > -SERVO_YAW_MAX_ANGLE){
				  yaw = yaw - MOVE_SPEED;
			  }
		  }
		  if(target_up()){
			  printf("Targeting up\r\n");
			  if(pitch > SERVO_PITCH_MAX_SAFE_ANGLE_MAX){
				  pitch = pitch - MOVE_SPEED;
			  }
		  }
		  if(target_down()){
			  printf("Targeting down\r\n");
			  if(pitch < SERVO_PITCH_MAX_SAFE_ANGLE_MIN){
				  pitch = pitch + MOVE_SPEED;
			  }
		  }
	  }else{
		  //Head towards origin (slowly lol)
		  if(pitch > 0){
			  pitch --;
		  }
		  if(pitch < 0){
			  pitch ++;
		  }
		  if(yaw > 0){
			  yaw --;
		  }
		  if(yaw < 0){
			  yaw ++;
		  }
	  }
	  printf("Attempting move to %d,%d\r\n", yaw, pitch);
	  set_gimbal_angles(yaw, pitch);
	  //----------------------STATE MACHINE LOGIC--------------------------
	  switch(state){
	  case START:
		  OpenLCD_clear();
		  OpenLCD_setCursor(0, 0);
		  OpenLCD_writestr(MESSAGE_SEARCHING);
		  if(sees_face() && !(target_down()||target_up()||target_left()||target_right())){
			  //We're centered.
			  printf("Transitioning state to CENTERED\r\n");
			  counter = 0; //We just saw someone
			  state = CENTERED;
		  }
		  break;
	  case CENTERED:
		  if(!sees_face() || (target_down()||target_up()||target_left()||target_right())){
			  counter++;
			  if(counter > RESET_TIMEOUT){
				  OpenLCD_clear();
				  state = START;
			  }
			  OpenLCD_clear();
			  OpenLCD_setCursor(0, 0);
			  OpenLCD_writestr(MESSAGE_SEARCHING);
			  break; //We're not seeing a face; don't even try to read temp
		  }else{
			  counter = 0;
		  }
		  //We're actively centered on a face still
		  //Read the temperature
		  MLX_read();
		  float temp = MLX_object();
		  float ambient = MLX_ambient();
		  char buf[100];
		  gcvt(temp, 8, buf);

		  if(temp > TEMP_THRESHOLD){
			  //We're pretty sure we're reading a forehead
			  //Show the temperature
			  OpenLCD_clear();
			  OpenLCD_setCursor(0, 0);
			  OpenLCD_writebuff(buf, 6);
			  if(temp < TEMP_SAFE){
				  //They're considered a safe temperature.
				  //Display it, and green
				  OpenLCD_setFastBacklightrgb(27, 240, 69);
				  state = PAUSE; //Give them some time to see it before clearing.
			  }else if(temp < TEMP_UNSAFE){
				  //Threshold temperature.
				  //Display it, and yellow, alongside instructions to touch contact sensor.
				  OpenLCD_setFastBacklightrgb(230, 255, 0);
				  OpenLCD_setCursor(0, 1);
				  OpenLCD_writestr(MESSAGE_TOUCH);
				  HAL_Delay(1500);
				  locked_temp = temp;
				  state = TOUCH_WAIT;
			  }else{
				  //Unsafe temperature.
				  //Display it, and red
				  OpenLCD_setFastBacklightrgb(240, 27, 105);
				  state = PAUSE;// Give them some time to see it before clearing.
			  }
		  }else{
			  printf("Detected temp is %f\r\n", temp);
			  OpenLCD_clear();
			  OpenLCD_setCursor(0, 0);
			  OpenLCD_writestr(MESSAGE_MOVE_CLOSER);
		  }

		  break;
	  case TOUCH_WAIT:
		  //The user isn't confirmed safe / unsafe; they're in-between
		  //Make them use the contact sensor for further evaluation
		  asm("nop");//Statement required after label.
		  float touch_temp = read_temperature_blocking();
		  char touch_buf[500];
		  gcvt(touch_temp, 8, touch_buf);
		  char locked_temp_buf[100];
		  gcvt(locked_temp, 8, locked_temp_buf);

		  OpenLCD_clear();
		  OpenLCD_setCursor(0, 0);
		  OpenLCD_writebuff(locked_temp_buf, 6);
		  if(touch_temp > TOUCH_TEMP_THRESHOLD){
			  counter = 0;
			  OpenLCD_setCursor(0, 1);
			  OpenLCD_writestr(MESSAGE_HOLD);
			  state = TOUCH_HOLD;
		  }else{
			  OpenLCD_setCursor(0, 1);
			  OpenLCD_writestr(MESSAGE_TOUCH);
			  counter++;
			  if(counter > TOUCH_TIMEOUT){
				 OpenLCD_clear();
				 OpenLCD_setFastBacklightrgb(128, 128, 128);
				 state = START;
			  }
		  }
		  break;
	  case TOUCH_HOLD:
		  counter++;
		  if(counter < TOUCH_HOLD_COUNT) break;
		  char locked_temp_buf2[100];
		  gcvt(locked_temp, 8, locked_temp_buf2);

		  OpenLCD_clear();
		  OpenLCD_setCursor(0, 0);
		  OpenLCD_writebuff(locked_temp_buf2, 6);






		  float touch_temp2 = read_temperature_blocking();
		  char touch_buf2[500];
		  gcvt(touch_temp2, 8, touch_buf2);

		  OpenLCD_setCursor(0, 1);
		  OpenLCD_writebuff(touch_buf2, 6);
		  if(touch_temp < TOUCH_TEMP_SAFE){
		 		//They're considered a safe temperature.
		 		//Display it, and green
		 		OpenLCD_setFastBacklightrgb(27, 240, 69);
		 		counter = 0;
		 		state = PAUSE; //Give them some time to see it before clearing.
		  }else{
			  //Unsafe temperature.
			  //Display it, and red
			  OpenLCD_setFastBacklightrgb(240, 27, 105);
			  counter = 0;
			  state = PAUSE;// Give them some time to see it before clearing.
		  }
		  break;
	  case PAUSE:
		  counter++;
		  if(counter > DELAY_TIMEOUT){
			  OpenLCD_clear();
			  OpenLCD_setFastBacklightrgb(128, 128, 128);
			  state = START;
		  }
		  break;
	  }


	  MLX_read();
	  float temp = MLX_object();
	  float ambient = MLX_ambient();
	  char buf[100];
	  gcvt(temp, 8, buf);
	  printf("Temp is %f\r\n", temp);

	  HAL_Delay(100);
  }
  /* USER CODE END 3 */
}

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
/* USER CODE BEGIN 4 */



#ifdef __GNUC__
#define PUTCHAR_PROTOTYPE int __io_putchar(int ch)
#else
  #define PUTCHAR_PROTOTYPE int fputc(int ch, FILE *f)
#endif /* __GNUC__ */
PUTCHAR_PROTOTYPE
{
  HAL_UART_Transmit(&huart2, (uint8_t *)&ch, 1, 0xFFFF);
  return ch;
}


/* USER CODE END 4 */
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


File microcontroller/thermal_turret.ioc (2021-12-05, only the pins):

Mcu.UserName=STM32F401RETx
PA1.Signal=ADCx_IN1
PA2.Signal=USART2_TX
PA3.Signal=USART2_RX
PA8.Signal=S_TIM1_CH1
PA9.Signal=S_TIM1_CH2
PB10.Signal=GPIO_Input
PB3.Signal=GPIO_Input
PB4.Signal=GPIO_Input
PB5.Signal=GPIO_Input
PB6.Signal=I2C1_SCL
PB7.Signal=I2C1_SDA
PC8.Signal=GPIO_Input

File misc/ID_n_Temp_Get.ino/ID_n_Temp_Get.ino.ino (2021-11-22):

/****************************************************************************** 
MLX90614_Get_ID.ino
Print ID register values stored in the MLX90614

This example reads from the MLX90614's ID registers, and 
prints out the 64-byte value to the serial monitor.

Hardware Hookup (if you're not using the eval board):
MLX90614 ------------- Arduino
  VDD ------------------ 3.3V
  VSS ------------------ GND
  SDA ------------------ SDA (A4 on older boards)
  SCL ------------------ SCL (A5 on older boards)
  
Jim Lindblom @ SparkFun Electronics
October 23, 2015
https://github.com/sparkfun/SparkFun_MLX90614_Arduino_Library

Development environment specifics:
Arduino 1.6.5
SparkFun IR Thermometer Evaluation Board - MLX90614
******************************************************************************/

#include <Wire.h> // I2C library, required for MLX90614
#include <SparkFunMLX90614.h> //Click here to get the library: http://librarymanager/All#Qwiic_IR_Thermometer by SparkFun
#include <SerLCD.h> //Click here to get the library: http://librarymanager/All#SparkFun_SerLCD


  SerLCD lcd; // Initialize the library with default I2C address 0x72
  IRTherm therm; // Create an IRTherm object to interact with throughout

void setup() 
{
  Serial.begin(115200); // Initialize Serial to log output
  Wire.begin(); //Joing I2C bus
  
  if (therm.begin() == false){ // Initialize thermal IR sensor
    Serial.println("Qwiic IR thermometer did not acknowledge! Freezing!");
    while(1);
  }
  Serial.println("Qwiic IR Thermometer did acknowledge.");
  
  therm.setUnit(TEMP_F); // Set the library's units to Farenheit
                         //  Alternatively, TEMP_F can be replaced with TEMP_C for Celsius or
                         //  TEMP_K for Kelvin.
  
  pinMode(LED_BUILTIN, OUTPUT); // LED pin as output

  //LCD
  lcd.begin(Wire); //Set up the LCD for I2C communication

  lcd.setBacklight(255, 255, 255); //Set backlight to bright white
  lcd.setContrast(0); //Set contrast. Lower to 0 for higher contrast.

  lcd.clear(); //Clear the display - this moves the cursor to home position as well
  lcd.print("Hello");

  therm.read();
}

void loop() 
{
  digitalWrite(LED_BUILTIN, HIGH);
    
  // Call therm.read() to read object and ambient temperatures from the sensor.
  if (therm.read()) // On success, read() will return 1, on fail 0.
  {
    // Use the object() and ambient() functions to grab the object and ambient
  // temperatures.
  // They'll be floats, calculated out to the unit you set with setUnit().
    Serial.print("Object: " + String(therm.object(), 2));
    Serial.println("F");
    Serial.print("Ambient: " + String(therm.ambient(), 2));
    Serial.println("F");
    Serial.println();

  // LCD
  // Set the cursor to column 0, line 1
  // (note: line 1 is the second row, since counting begins with 0):
  
  if (therm.object() > 77){
    lcd.setFastBacklight(255, 0, 0); //Set backlight to bright white
    lcd.setCursor(0, 1);
    // Print the number of seconds since reset:
    lcd.print("Temperature: " + String(therm.object(), 2) + "F");
    lcd.setCursor(0,0);
    lcd.print("Ambient: " + String(therm.ambient(), 2) + "F");
  }
  else {
    lcd.setFastBacklight(0,255,0);
    lcd.setCursor(0, 1);
     // Print the number of seconds since reset:
    lcd.print("Temperature: " + String(therm.object(), 2) + "F");
    lcd.setCursor(0,0);
    lcd.print("Ambient: " + String(therm.ambient(), 2) + "F");
  }


    
  }
  digitalWrite(LED_BUILTIN, LOW);
  delay(100);
}

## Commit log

2021-11-16 Initialize STM32 project
2021-11-17 added laser cad
    [Camera-Laser.scad]
2021-11-17 added measurements
    [Camera-Laser.scad]
2021-11-17 Add empty directory for jetson code
2021-11-20 setup file for jetson nano
2021-11-21 camera set up
2021-11-21 split file into modules
    [camera-module.scad, laser-module.scad]
2021-11-21 preliminary STL's created
    [base-test.stl, camera-test.stl, laser-module-test.stl]
2021-11-21 added turret setup
    [Camera-Laser.scad]
2021-11-21 Updated stl for better printing
    [camera-test.stl]
2021-11-21 updated laser module
    [Camera-Laser.scad, laser-module.scad]
2021-11-22 (Not working) basic SMBus start
    [main.c, thermal_turret.ioc]
2021-11-22 Basic servomotor control code
2021-11-22 Add CV logic and output pin to detect lack of face
2021-11-22 Rework CV code to make it more accurate at determining next move
    [webcam_record.py]
2021-11-22 Create webcam_record_headless.py file
    When OpenCV calls the "imshow" function, it crashes the program if there is
    no window present.
    Because we want to run this file as a headless cron job (which won't have a
    attached window or display), I created a copy of the code which is the same
    except for the imshow removed.
    A better solution would be to create a command-line flag or something, but
    I'm lazy lol.
    [webcam_record_headless.py]
2021-11-22 fixed measurements
    [Camera-Laser.scad, camera-module.scad, laser-module.scad]
2021-11-22 generated new stl tests
    [base-test-1.stl, camera-test-1.stl, camera-test-2.stl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]
2021-11-24 Finish set_gimbal_angles function, measure real ranges of servos
2021-11-24 Move gimbal initialization code to dedicated function, comment out LCD driver temporarily to avoid compile error
    [main.c]
2021-11-24 Add servo wiring documentation, minor change to README.md
2021-11-24 Fix formatting of wiring.md
2021-11-24 Add laser wiring documentation, not working SMBus test code
2021-11-25 added GPIO pins to the jetson nano, with four pins
2021-11-25 Switched smbus to i2c
2021-11-27 Wiring update
2021-11-27 More basic ADC testing stuff
2021-11-27 Better thermometer experimental code, printf support (with floats\!)
2021-11-28 trying to fix I2C
    [main.c]
2021-12-01 Basic fully working temperature reading with contact sensor :D
2021-12-01 Move logic for reading temperature sensor into dedicated driver function
2021-12-01 Add newline and carriage return to MLX90614 library error printfs to make log output cleaner
    [MLX90614.c]
2021-12-01 Fix struct used for i2c fix function
    [main.c]
2021-12-03 Update wiring.md doc
2021-12-03 Modify IOC to set GPIO input pins and add Rutvi+Abdul's basic gimbal driver code
2021-12-03 Minor encapsulation of gimbal vision interface drivers
2021-12-03 Update wiring.md, i2c is maybe possibly working???
2021-12-04 added csv's and matlab
    [Arduino.csv, STM32.csv]
2021-12-04 reset ARduino code
2021-12-05 Add logic for sees face output pin
2021-12-06 Update for newer camera
    [C270Bracket.scad, Camera-Laser.scad, laser-module.scad]
2021-12-06 cad update
    [Camera-Laser.scad]
2021-12-06 Undid my mistakes
    [Camera-Laser.scad]
2021-12-07 STL made for full base 1
    [Full-test1.stl]
2021-12-07 Added touch sensor read if temp too high
    [main.c]
2021-12-08 fixed camera directions
2021-12-08 V2 turret design
    [Camera-Laser.scad, Full-test1 - v2.stl]
2021-12-09 Switch to HAL_Delay, making wait times much more reasonable
2021-12-09 Add state to account for slow touch sensor
2021-12-09 Fix small mistake preventing compile
    [main.c]
2021-12-09 Some cad updates
    [C270Bracket.scad, Camera-Laser.scad, case.scad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]
2022-05-03 Updated 3d Models
    [C270Bracket.scad, Camera-Laser.scad, camera-module.scad]

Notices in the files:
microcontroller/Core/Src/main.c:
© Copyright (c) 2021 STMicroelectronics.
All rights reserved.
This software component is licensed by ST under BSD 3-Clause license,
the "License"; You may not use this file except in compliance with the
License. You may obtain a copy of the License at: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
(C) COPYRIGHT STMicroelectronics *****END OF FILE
